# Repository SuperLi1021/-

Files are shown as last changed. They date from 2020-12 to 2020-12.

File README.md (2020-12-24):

# 检测室内外温度值控制小风扇的设计报告

### 1.题目要求

> ### 1. 最低要求
>
>  
>
> a) 当室内温度大于室外温度时，小风扇转动；当室内温度低于室外温度时，小风扇静止。
>
> b) 利用纸箱等材料搭建演示模型（纸箱大小不小于30x*30*x15CM）。
>
> 
>
> c) 提交一份纸质的设计报告（字数 400 字以上）。
>
>  
>
> ## 2. 基本要求
>
> a) 采用 51 内核或ARM Cortex 内核（stm32 等）单片机进行控制。
>
> b) 当室内处于较低温度时，小风扇不开启，可通过按键手动开启风扇或改变风扇转速。转速分类不小于 4 档，变化明显。使用数码管等显示器件显示档位。
>
> c) 能显示室内外温度值。
>
> d) 当温度高于 30℃时，有声光报警提示（蜂鸣器可以不用），灯光需以呼吸灯形式提醒，即灯逐渐亮，逐渐暗，亮灭持续时间随温度增加而缩短，肉眼可明显区分，当温度高于 30℃+5℃时灯变为闪烁，闪烁周期不小于 0.25s。（温度值可根据调试情况自行调整，调整区间为±5℃）
>
> ## 3. 发挥部分
>
> a) 根据室内温度，自动调整小风扇转速，温度升高 1℃， 风扇转速加快一档。
>
> b) 在不重新编程的情况下，能调整声光报警阈值，并且断电不丢失。
>
> c) 设计遥控端，采用无线方式与控制端进行连接通信。遥控端能实时显示室内外温度、小风扇转速，并且能在遥控端控制小风扇的运行状态。
>
>
> d) 自行设计电机驱动电路（全分立器件）。

### 2.器件选型

需求：1.单片机

			1）产生波特率，电机pwm调速，呼吸灯，共三个定时器。

			2）在不重新编程的情况下，能调整声光报警阈值，并且断电不丢失。eeprom。

					因此单片机使用89c52rc

			2.远程通讯

			1）设计遥控端，采用无线方式与控制端进行连接通信。遥控端能实时显示室内外温度、小风扇转速，并且能在遥控端控制小风扇的运行状态。

			使用hc-05蓝牙模块。

			3.显示模块

			1）能显示室内外温度值。

			2）显示电机档位。

			3）显示设定的高低温阈值。

			使用lcd1602。

			4.测温模块

			测温使用ds16b20模块。

			5.电机驱动模块

			使用8050与8550三极管与1n4148搭建的H桥电路

### 3.程序框架



### 4.按键说明

| 按键 | 功能 |
| ---- | --- |
| 1 | 控制sw+1 如果sw>5,则sw=0 |
| 2 | + |
| 3 | - |

| sw | +说明 | -说明 |
| ---- | --- | --- |
| 0 | | 运行状态 |
| 1 | 低温阈值+1 | 低温阈值-1 |
| 2 | 高温阈值+1 | 高温阈值-1 |
| 3 | 电机占空比+10（绝对） | 电机占空比-10（绝对） |
| 4 | 电机启动（绝对） | 电机停止（绝对） |
| 5 | | 清空绝对状态 回归自动控制 |

### 5.蓝牙命令说明

| 命令（16进制） | 内容 |
| --- | --- |
| Aa bc | 高温阈值设为abc |
| Ba bc | 低温阈值设为abc |
| Ca bc | 占空比设为abc |
| Da bc | 频率设置为abc |
| E*** | 电机启动（绝对） |
| F*** | 电机关闭（绝对） |
| 00 00 | 仅查询系统状态 不改变参数 |
| 99 99 | 回到自动控制状态 |

### 6.显示说明

第二行16位分别为

| 位数 | |
| --- | --- |
| 1 2 3 | 室外温度（3位精度0.1） |
| 4 5 6 | 室内温度（3位精度0.1） |
| 7 8 9 | 低温阈值（3位精度1） |
| 10 11 12 | 高温阈值（3位精度1） |
| 13 | sw |
| 14 15 | 电机占空比（2位） |

### 7.温度测试模块说明

使用两个ds18b20作为温度传感器，采用单独接线方式，使用700毫秒的低电平脉冲作为初始化信号，然后进行写操作，读操作，温度转化操作，在此过程中，关闭中断以保证在此过程中的时序不受影响。

### 8.电机驱动模块说明

电机使用一个小型直流电机，驱动电机所用的电压电流并不大，所以使用三极管与二极管搭建H桥电路作为电机驱动电路。



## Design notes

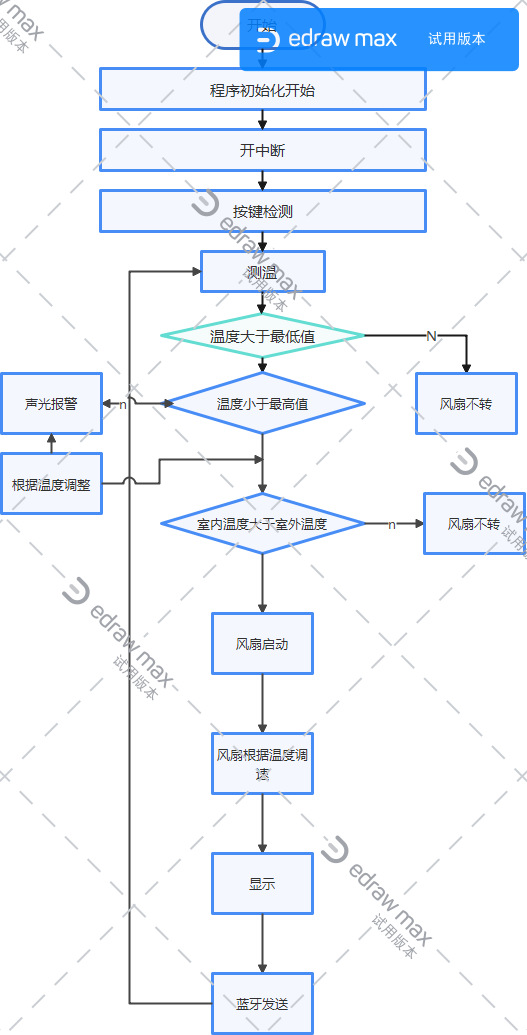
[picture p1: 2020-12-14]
简要流程图/程序流程图.png

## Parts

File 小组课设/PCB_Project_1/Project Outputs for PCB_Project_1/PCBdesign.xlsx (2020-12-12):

Comment | Description | Designator | Footprint | LibRef | Quantity
33P | 直插瓷片电容 | C1, C2 | CC 1.8*3.6 | C-CC | 2
104 | Capacitor | C3,C4, C5 | RAD0.1 | 普通电容 | 2
N4007 | 整流二极管 | D1 | DO-41 | 1N4007 | 1
IN4148 |  | D9, D10, D12, D13 | DIODE_SOP | IN4148 | 4
10uF/16V | Capacitor | E1 | CAP_2 | 电解电容 | 1
470 | Capacitor | E2 | CAP_2 | 电解电容 | 1
6x6x5 | 直插6x6轻触开关 | K1, K2, K3, SW1 | TSW DIP-6*6*6 | TSW DIP-6x6 | 4
LCD 1602 | LCD 1602 | LCD1 | LCD-1602 | LCD 1602 | 1
LED | LED | LED1 | LED-D5 | LED | 1
蓝色 | 5mm插件LED | LED3 | LED 5MM-G | LED-5MM | 1
HDR-1X2 | 2P接插件 | M1 | HDR2.54-LI-2P | Header 2 | 1
HC-05 | Header, 4-Pin | P1 | HDR1X4 | Header 4 | 1
POWER |  | P11 | COM2-2.54 | COM2-2.54 | 1
COM3-2.54 |  | P12, P14 | COM3-2.54 | COM3-2.54 | 2
XZ | Header, 4-Pin | P13 | HDR1X4 | Header 4 | 1
S8050 | NPN | Q1, Q2, Q13, Q14 | TO-92 | S8050 | 4
S8550 | PNP | Q15, Q16 | TO-92 | S8550 | 2
1K | 直插色环电阻 | R1, R6 | RS 1/4W | R-CRR | 2
103 | 单列直插排阻 | R2 | R SIP9-2.54 | R SIP9 | 1
1K | Resistor | R28, R29, R30, R31, R32 | RES-0.25W-6.5X2.5-10.16-0.6 | RES | 5
10K | 插件单联电位器 | RP1 | 3296W | RP-ID | 1
POWER | 1路单刀船型开关 | S2 | KCD1-101 | KCD1-101 | 1
STC89C5xx | STC单片机 | U1 | DIP40-600 | STC89C5xx | 1
11.0592MHz | 2脚无源脚晶振 | Y1 | OSC HC-49S | XTAL-2P | 1

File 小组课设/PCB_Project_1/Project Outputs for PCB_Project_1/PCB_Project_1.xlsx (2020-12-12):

Comment | Description | Designator | Footprint | LibRef | Quantity
33P | 直插瓷片电容 | C1, C2 | CC 1.8*3.6 | C-CC | 2
Cap | 104 | C3, C4, C5 | RAD-0.3 | Cap | 3
N4007 | 整流二极管 | D1 | DO-41 | 1N4007 | 1
10uF/16V | 直插电解电容 | E1 | CAP 1.5*4*8 | C-CAP | 1
470 | 直插电解电容 | E2 | CAP 1.5*4*8 | C-CAP | 1
6x6x5 | 直插6x6轻触开关 | K1, K2, K3, SW1 | TSW DIP-6*6*6 | TSW DIP-6x6 | 4
LCD 1602 | LCD 1602 | LCD1 | LCD-1602 | LCD 1602 | 1
蓝色 | 5mm插件LED | LED3 | LED 5MM-G | LED-5MM | 1
HC-05 | Header, 4-Pin | P1 | HDR1X4 | Header 4 | 1
POWER |  | P11 | COM2-2.54 | COM2-2.54 | 1
COM3-2.54 |  | P12 | COM3-2.54 | COM3-2.54 | 1
XZ | Header, 4-Pin | P13 | HDR1X4 | Header 4 | 1
1K | 直插色环电阻 | R1, R6 | RS 1/4W | R-CRR | 2
103 | 单列直插排阻 | R2 | R SIP9-2.54 | R SIP9 | 1
10K | 插件单联电位器 | RP1 | 3296W | RP-ID | 1
POWER | 1路单刀船型开关 | S2 | KCD1-101 | KCD1-101 | 1
STC89C5xx | STC单片机 | U1 | DIP40-600 | STC89C5xx | 1
HDR-1X4 | 4P接插件 | WAVE | HDR2.54-LI-4P | Header 4 | 1
11.0592MHz | 2脚无源脚晶振 | Y1 | OSC HC-49S | XTAL-2P | 1

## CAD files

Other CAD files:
output/main.obj
output/lanya.obj
project/anjian.obj
output/anjian.obj
output/ds18b20.obj
output/lcd1602.obj
output/EEPROM.obj
output/Text1.obj
output/delay.obj
output/Bluetooth.obj
output/STARTUP.obj
output/temp 1.obj
output/display.obj
output/temp.obj

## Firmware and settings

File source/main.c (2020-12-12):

#include "eeprom.h"
#include <reg52.h>
#include <string.h>
#include <intrins.h>
#include "lcd1602.h"
#include "anjian.h"
#include "delay.h"
#include "lanya.h"
#define uchar unsigned char
#define uint unsigned int
#define FOSC 11.0592 // 系统晶振频率11.0592MHz

/*distance   表示此次加药剂量
m时间间隔
l模式
h次数
zkb占空比
pl 频率
FACTOR流量计算系数
*/



	
/*主模块端口定义*/
sbit pwm = P2^1; // 电平触发输入引脚






/*主模块函数声明*/
void computeDis();

 
 
uchar TxStr[3] = {0};
uchar dat[2] ={0x01,0x02};



/*定义全局变量*/
uint distance = 0; // 存放距离
unsigned int sw,l,m,h,d,ll,tingzhi,tingzhis,shijian, FACTOR,zkb,pl,pwmt,quanshu,yunxing;
/*distance   表示此次加药剂量
m时间间隔
l模式
h次数
zkb占空比
pl 频率
FACTOR流量计算系数
tingzhi 间隔标志
tingzhis 间隔时间
shijian 单片机运行实际时间
dj 不记pwm情况下的电机启动
外部中断0 跳沿触发 计算圈数
定时器0  计时
定时器1 产生波特率
定时器2 pwm调速
实际流量=圈数*流量计算系数

*/
 uchar djb;

/*主函数*/
void main(){
	uchar bz =0;
	quanshu=0;
	pl=100;//1khz
	zkb=50;//30%
	pwmt=0;
	tingzhis=0;
	tingzhi=0;
	shijian=0;
	l=100;
	m=20;
	h=10;
	sw=0;

	dj=0;

	yunxing=0;
	LCDInit();
	timerInit();
 	FACTOR=115; 
/*eeprom	
    SectorErase(0x2000);    //擦除第一扇区
    byte_write(0x2001,dat[0]);   //在地址为0x2001的内存写入一个字节
    byte_write(0x2002,dat[1]);   //在地址为0x2002的内存写入一个字节
    delay(1000);       //延时1s
    TxStr[0] = byte_read(0x2001);     //从地址0x2001读取一个字节
        TxStr[1] = byte_read(0x2002);     //从地址0x2002读取一个字节
 

 
        delay(2000);        //延时2s
  */
    while(1)
    { 
       

	
	if(yunxing==1)

{

		if(tingzhi==1)
	{	
	if(bz==0)
	 {tingzhis=shijian;//计算停止时间
		bz=1;
		}

	if((shijian-tingzhis)>=m)
	{
	tingzhi=0;//停止标志位恢复
	bz=0;
	}
	}


	computeDis();		//计算
	if(tingzhi==0)
	{	if(h>0)
		{
			
					
			if(distance<l)
			{dj=1;
			delay(1);
			}
			if(distance>=l)
			{	
				dj=0;
				delay(1);
				h=h-1;
				tingzhi=1;
			}
		}
	}

}
	display(distance,l,m,h);		// 显示流量 模式l 时间间隔m 次数h 
     anjian();

		}
	
		if(djb==1)
			{
					dj=1;
					delay(50);
			}
			if(djb==0)
			{
					dj=0;
					delay(10);
			}
}





/*void timer0Service() interrupt 1{  // 定时器0中断    秒计时
	
static uint ii=0;

	TH0 = 0x4c;
	TL0 = 0x00;
	ii++;
	if(ii==20)
	{ii=0;
	shijian++;
	}

	}


	*/





/*timer2溢出中断服务程序*/
void timer2Service() interrupt 5{  // pwm调速

	TF2=0;
	pwmt++;
	
if(pwmt>=pl) //1khz
 
pwmt=0;
 
if(pwmt<=zkb) //占空比%30,可改
 
pwm=1;
 
if(pwmt>zkb) pwm=0;
 


}


/*pwmt pwm调速中的时间
zkb   占空比
pl 频率
pwm 电机实际输出
TF2 定时器2 溢出重置
*/


/*模式 ：5 / 10 / 15
加药速度：
计量
加料时间
次数
*/

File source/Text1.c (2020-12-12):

//显示 室外温度 室内温度 温度阈值 占空比
//蓝牙发送 室外温度 室内温度 温度阈值 占空比
//蓝牙接收 阈值 占空比
//按键 1选择 2加 3减
//定时器1 9600波特率 定时器2 pwm
//定时器0 



#include "eeprom.h"
#include <reg52.h>
#include <string.h>
#include <intrins.h>
#include "lcd1602.h"
#include "anjian.h"
#include "delay.h"
#include "lanya.h"
//#include "temp.h"
//#include "temp 1.h"
#include "ds18b20.h"
#define uchar unsigned char
#define uint unsigned int
#define FOSC 11.0592 // 系统晶振频率11.0592MHz

/*distance   表示此次加药剂量
m时间间隔
l模式
h次数
zkb占空比
pl 频率
FACTOR流量计算系数
*/



	
/*主模块端口定义*/
//sbit pwm = P1^7; // 电机实际动作
sbit pwm = P2^1; // 电机实际动作
sbit aaa=P2^0;
sbit led1 = P2^2; // 声光报警





/*主模块函数声明*/

static uint iiii=0;/*定义全局变量*/ 
uchar TxStr[3] = {0};
uint wenduo = 0; // 温度
uint wendui = 0; // 温度
unsigned int sw,d,ll,pl,pl1,pwmt,led,yunxing;	
uchar djb,gaowen,diwen,zkb,zkb2,dj,zkbb,djbb;
uint zkb1;//led 呼吸灯占空比
uint bz;//回头标志
uint w35;//温度是否高于35度
/*distance   表示此次加药剂量
m时间间隔
l模式
h次数
zkb占空比
pl 频率
shijian 单片机运行实际时间
dj 不记pwm情况下的电机启动
外部中断0 跳沿触发 计算圈数
定时器0  计时
定时器1 产生波特率
定时器2 pwm调速
实际流量=圈数*流量计算系数

*/


/*主函数*/
void main(){
	pl1=400;//1khz
	pl=8;
	zkb=50;//30%
	zkb1=0;
	aaa=1;
	delay(10);
	zkb2=50;
	pwmt=0;
	gaowen=30;
	diwen=15;
	sw=0;
	dj=1;
	djb=0;
	djbb=0;
	zkbb=0;
	yunxing=1;
	LCDInit();
	timerInit();

/*eeprom	*/



 TxStr[0] = byte_read(0x2001);     //从地址0x2001读取一个字节
    TxStr[1] = byte_read(0x2002);     //从地址0x2002读取一个字节
 diwen=TxStr[0];
	gaowen=TxStr[1];

 
    delay(200);        //延时2s

    while(1)
    { 	/*	EA=0;
					wenduo= Ds18b20ReadTemp()-100 ;

       	 	wendui= Ds18b20ReadTemp1()-100 ;
			
	
					EA=1;*/
					wenduo= temper_change1()/10;

       	 	wendui= temper_change2()/10;

	if(yunxing==1)	//程序允许运行
	{	if(zkbb==0&&djbb==0)
		{if(wendui>diwen*10)	  //室内温度大于低温阈值
		{	if(wendui>wenduo) //室内温度大于室外温度
			{ dj=1;			  //电机标志启动
				zkb=(wendui-diwen*10)/3;
				if(zkb>=90) zkb=90;
			 }

		}
	
		if(wendui<wenduo)		   //室内温度低于室外温度
		{dj=0;					   //关电机
		}

	}
		if(wendui>gaowen*10)		   //	  温度高于阈值 报警
		{	led=1;zkb2=2+(wendui/10-gaowen);
			}
		if(wendui<gaowen*10)		   //	  温度低于阈值 停止报警
		{	led=0;
			}
		if(wendui>350)		   //	  温度>35 标志
		{	w35=1;
			}
		if(wendui<350)		   //	  温度<35 标志
		{	w35=0;
			}
		
		


	}
	display(wenduo,wendui,diwen,gaowen,zkb,sw);		// 室外温度 室内温度 低温阈值 高温阈值 电机占空比
     anjian();

		
	





		if(dj==1)
			TR2=1;
		if(dj==0) 
			{TR2=0;
			 pwm=1;
			 }
			if(djb==1)
			{
					dj=1;
					delay(50);
			}
			if(djb==0)
			{
					dj=0;
					delay(10);
			}
		
		if(led==1)
		{  TR0=1 ;
			}
		if(led==0)
		{  TR0=0;
			led1=0;
			}
if(diwen!=TxStr[0]||gaowen!=TxStr[1])
  {
    SectorErase(0x2000);    //擦除第一扇区
   byte_write(0x2001,diwen);   //在地址为0x2001的内存写入一个字节
    byte_write(0x2002,gaowen);   //在地址为0x2002的内存写入一个字节
    delay(200);       //延时1s
	}



}
}




void timer0Service() interrupt 1{  // 定时器0中断    秒计时
	



	TH0 = (65535 - 900) / 256;
	TL0 = (65535 - 900) % 256;
	iiii++;
	if(w35==0){
		
	if(zkb1>=900)
	{bz=1;

	}

	if(zkb1<=200)
	{bz=0;
	}

	if(iiii>=pl)
	{iiii=0;

	if(bz==1)zkb1=zkb1-zkb2;
	if(bz==0)zkb1=zkb1+zkb2;
	 
	 
	}
   
	

	if(iiii>zkb1/100)
	{	led1=0;
	}
	if(iiii<zkb1/100)
	{led1=1;
	 }
 }
	if(w35==1)
	{if(iiii>450)
		iiii=0;
		if(iiii<0.5*450)led1=0;
		if(iiii>0.5*450)led1=1;
	}


}




/*timer2溢出中断服务程序*/
void timer2Service() interrupt 5{  // pwm调速

	TF2=0;
	pwmt++;
	
if(pwmt>=pl1) //1khz
 
pwmt=0;
 
if(pwmt<=zkb*4) //占空比%30,可改
 
pwm=0;
 
if(pwmt>zkb*4) pwm=1;
 


}


/*pwmt pwm调速中的时间
zkb   占空比
pl 频率
pwm 电机实际输出
TF2 定时器2 溢出重置
*/


/*模式 ：5 / 10 / 15
加药速度：
计量
加料时间
次数
*/

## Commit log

2020-12-12 原理图和pcb
    [PCB1.PcbDoc, PCB_Project_1.PrjPcb, PCB_Project_1.xlsx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]
2020-12-12 电机与呼吸灯调试后
    [EEPROM.obj, Text1.obj, anjian.obj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]
2020-12-14 完整版 附带设计说明
    [Bluetooth.obj, EEPROM.obj, STARTUP.obj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]
2020-12-24 修改说明
